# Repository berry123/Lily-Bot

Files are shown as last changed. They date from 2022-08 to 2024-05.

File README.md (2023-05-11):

# Flower-Bots
This GITHUB as well as the one on YouTube, Instructables, Hackster and Rose-Hulman (https://wordpress.rose-hulman.edu/berry123) will document my guidebook for members of academia to use open-source hardware for service, education, and research. It will describe the creation of an open-source mobile robot platform with the flexiblity and modularity for modification based upon experience level, educational, outreach, or research goals.

https://www.oshwa.org/2022/06/15/congratulations-to-the-open-hardware-trailblazers/

OSHWA recently announced a call for Open Hardware Trailblazer Fellows. Thanks to the generous support of the Alfred P. Sloan Foundation, OSHWA is taking a giant step towards expanding open source hardware in academia through the Open Hardware Trailblazer Fellows initiative. The one-year fellowship provides grants to individuals who are leading the way as open source hardware expands into academia. The fellows will document their experience of making open source hardware in academia to create a library of resources for others to follow.

Carlotta Berry is a professor and Dr. Lawrence J. Giacoletto Endowed Chair for Electrical and Computer Engineering at Rose-Hulman Institute of Technology (RHIT). She is one of a team of faculty who created the first multidisciplinary minor in robotics. She has two bachelor’s degrees in mathematics from Spelman College and electrical engineering from Georgia Institute of Technology. She has a master’s from Wayne State University and PhD from Vanderbilt University. Her research interests include robotics education, human-robot interaction, and increasing marginalized and minoritized populations in STEM fields. Berry is a prolific speaker and author of the text, “Mobile Robotics for Multidisciplinary Study”. Berry is also the founder and co-director of the Rose Building Undergraduate Diversity (ROSE-BUD) Program and advisor for the National Society of Black Engineers. She was previously the President of the Technical Editor Board for the American Society of Engineering Education (ASEE) Computers in Education Journal, ASEE fellow and IEEE senior fellow. She has a special passion for diversifying the engineering profession by encouraging more women, marginalized and minoritized populations to pursue STEM degrees. She achieves this purpose with robotics education, engineering education and human-robot interaction research to bring more people to STEM. Her strong service record has garnered her multiple accolades and awards including 2023 IEEE Undergraduate Teaching Award, Society of Women Engineers 2022 Distinguished Engineering Educator Award, 2022 Distinguished Educator Award from the American Society of Engineering Education Electrical and Computer Engineering Division, 2022 Open Source Hardware Trailblazer Fellow, 2021 TechPoint Foundation for Youth Bridge Builder award, one of 30 Women in Robotics You Need to Know About 2020 by robohub.org, Reinvented Magazine Interview of the Year Award on Purpose and Passion, FIRST Indiana Robotics Gamechanger Award 2020, Women and Hi Tech Leading Light You Inspire Me Award 2018 and Insight Into Diversity Inspiring Women in STEM. During 2020, she worked with colleagues around the world to start two non-profit organizations, Black In Engineering and Black In Robotics. They have a mission to bring awareness to systemic racism and inequity in STEM, build community, advocate for diversity, equity, inclusion, justice, and connect with allies and sponsors.

oshw_facts

This project is certified open hardware.

OSHW Certified_xsmall

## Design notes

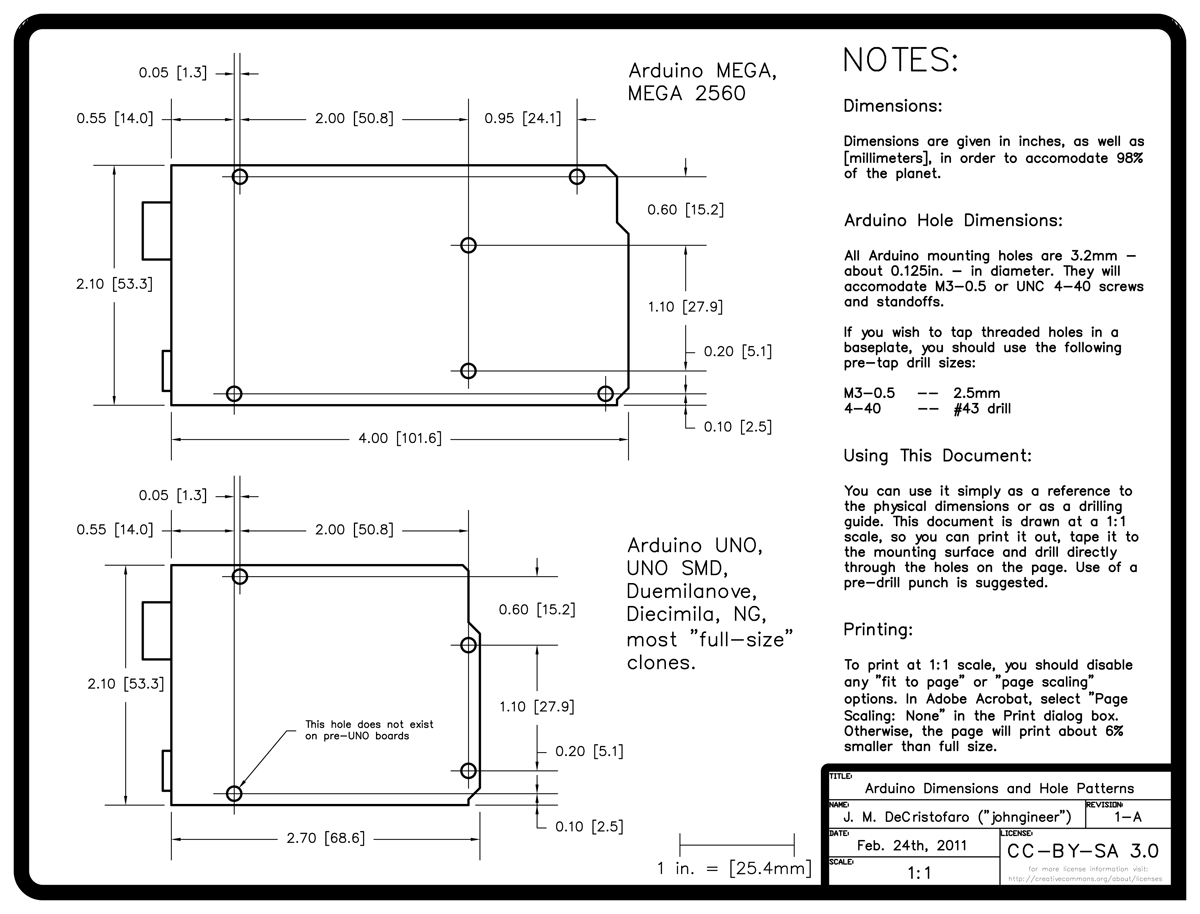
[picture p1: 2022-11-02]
Flower bots/Assembly/Uno and Mega schematics.png

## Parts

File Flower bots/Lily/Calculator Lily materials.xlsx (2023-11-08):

Input number of Lilys | 16
 |  | Part | Need | Have | Total |  | Part | Time/part (h) | Time to print (h) | Material/part (g) | Total material (g)
 | 3D Printer | Tops | 16 |  | 16 | 3D Printer | Tops | 3.50 | 56.00 | 37.36 | 597.76
 |  | Uno cover | 16 |  | 16 |  | Uno cover | 1.50 | 24.00 | 16.19 | 259.04
 |  | Bottom | 16 |  | 16 |  | Bottom | 5.00 | 80.00 | 53.36 | 853.76
 |  | Battery cover | 16 |  | 16 |  | Battery cover | 1.33 | 21.28 | 16.48 | 263.68
 |  | Motor mounts | 32 |  | 32 |  | Motor mount
 |  | Sonar mounts | 16 |  | 16 |  | Sonar mounts
 |  | (IR photo resistor mount | 16 |  | 16 |  | IR/photoresistor mounts
 |  | Standoffs | 64 |  | 64 |  | Standoffs | 0.43 | 27.71 | 2.29 | 146.496
 | Shopping | Motor controller | 32 |  | 32 |  | Total | - | 208.99 | - | 2120.736
 |  | Uno chip | 16 |  | 16
 |  | 9V battery holder | 16 |  | 16
 |  | Mini breadboards | 32 |  | 32
 |  | Caster wheels | 32 |  | 32
 |  | Motors | 32 |  | 32
 |  | Toy wheels | 32 |  | 32
 |  | Buzzers | 16 |  | 16
 |  | Sonar | 16 |  | 16
 |  | Male wires | 0
 |  | Female wires | 0
 |  | LEDs | 64 |  | 64
 |  | 220 Resistors | 64 |  | 64
 |  | photoresistors | 16 |  | 16
 |  | 10K resistors | 16 |  | 16

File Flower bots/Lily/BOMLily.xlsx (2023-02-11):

Part ID# | Product | Qty. | Price ind | Price total | Link
# | Upper Chassis | 1 | 7.00 | 7.00
# | Lower Chassis | 1 | 1.17 | 1.17
# | Standoffs | 4 | 1.62 | 6.48
 | TB6612 Motor Driver | 1 |  | 0.00
 | Arduino Uno | 1 | 6.26 | 6.26
 | Mini Breadboard | 2 |  | 0.00
# | Motor Mounts | 2 |  | 0.00
 | Toy Motors | 2 |  | 0.00
 | Toy Tire Wheels | 2 |  | 0.00
 | 5AA Battery Holder | 1 |  | 0.00
 | Cinch strap | 1 |  | 0.00
 | Caster Wheels 5/8” | 2 |  | 0.00
# | Sonar Mounts* | 2 |  | 0.00
 | HC-SR04 Sonar * | 1 |  | 0.00
# | IR Mounts* | 1 |  | 0.00
 | Sharp IR Sensor* | 1 |  | 0.00
 | LEDs* | 4 |  | 0.00
 | Buzzer* | 1 |  | 0.00
 | Slider Switch* | 1 |  | 0.00
 | Photoresistor* | 1 |  | 0.00
 | 10kΩ resistor* | 1 |  | 0.00
 | 100Ω resistor* | 4 |  | 0.00
 | Various Wires (Male-Male, Male-Female) | 20 |  | 0.00
 | 6mm panhead screws | 2 |  | 0.00
 | 8 mm panhead screws | 8 |  | 0.00
 | 25mm panhead screws | 2 |  | 0.00
 | Phillips head screwdriver | 1 |  | 0.00
 |  |  | Total: | 20.91

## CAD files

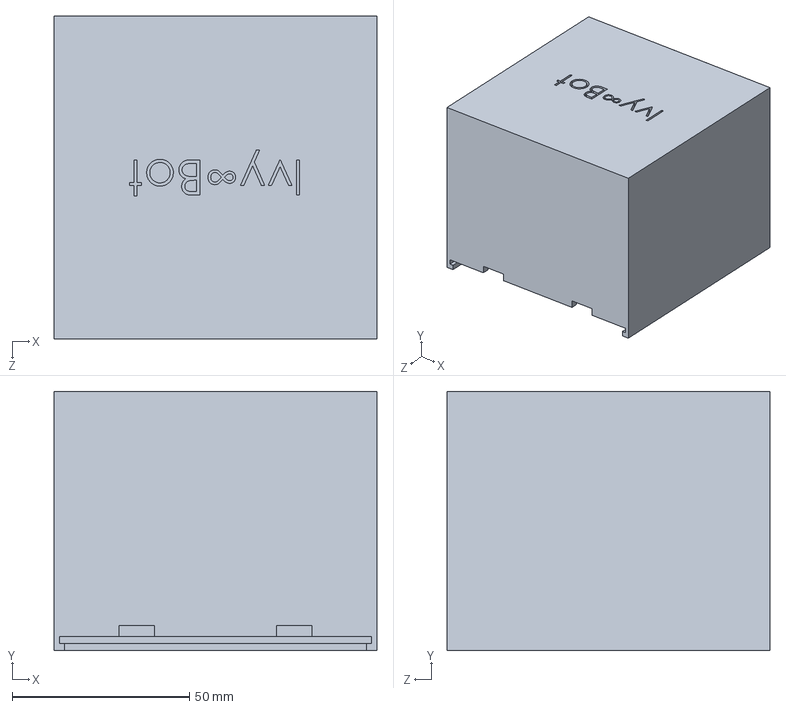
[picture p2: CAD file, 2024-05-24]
Flower bots/Ivy bot/Main box.SLDPRT
91.0 x 73.0 x 91.0 mm

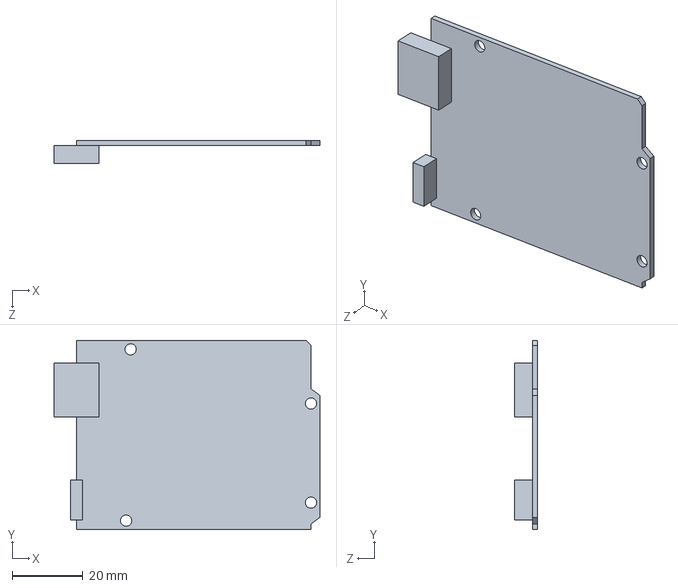
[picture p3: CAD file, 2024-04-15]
Flower bots/Assembly/Uno chip.SLDPRT
74.9 x 53.3 x 6.58 mm

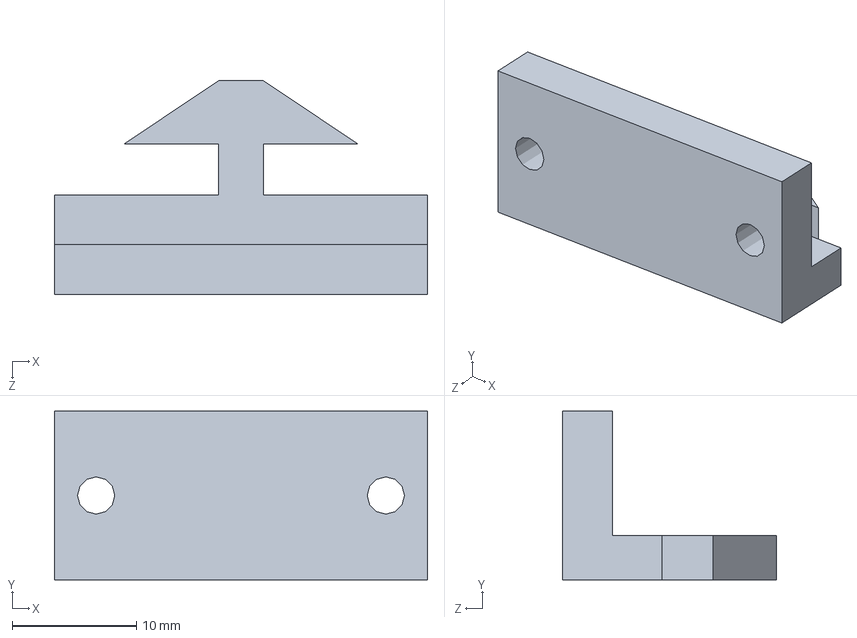
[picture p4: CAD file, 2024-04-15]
Flower bots/Attachments/SolidWorks/Gripper attachment.SLDPRT
30.0 x 13.6 x 17.2 mm

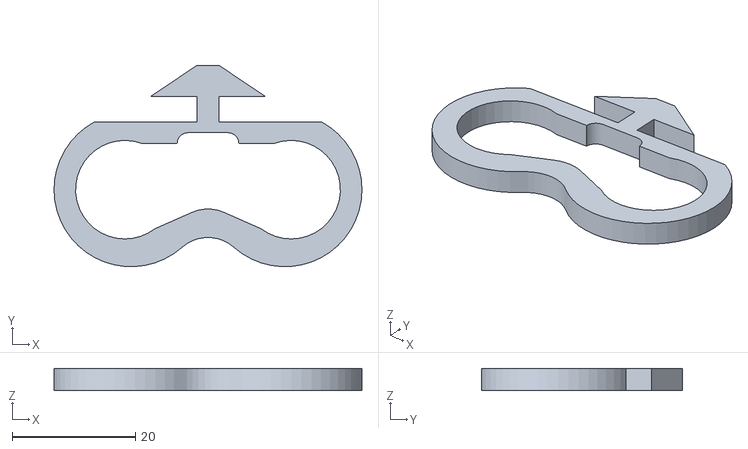
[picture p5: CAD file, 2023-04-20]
Flower bots/Attachments/STL/Sonar sensor Attachment .STL
50.0 x 32.7 x 3.58

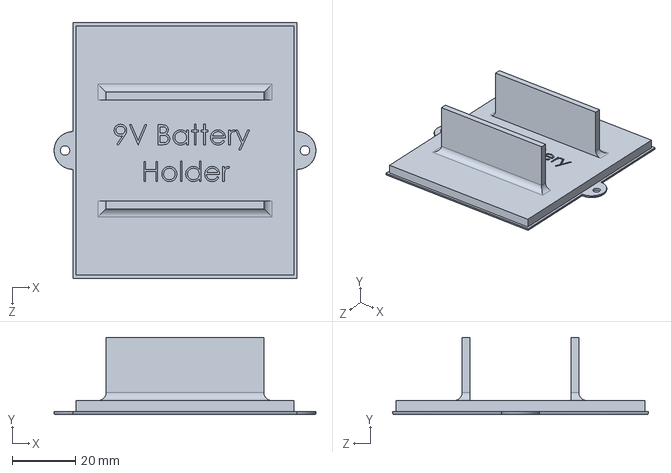
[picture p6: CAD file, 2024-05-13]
Flower bots/Battery modules/SolidWorks/9V Battery Holder New.SLDPRT
83.0 x 24.5 x 81.0 mm

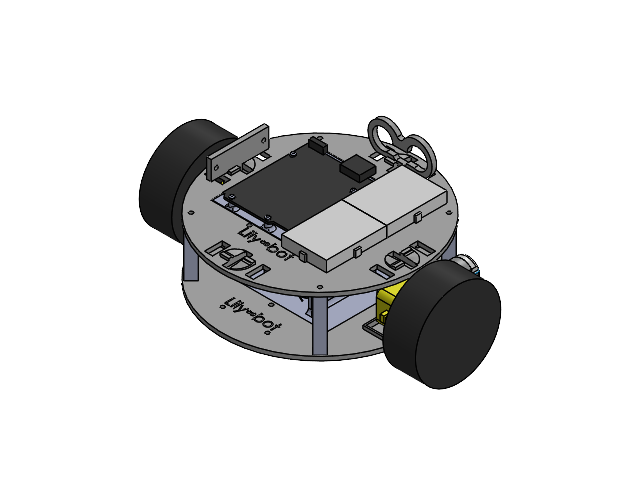
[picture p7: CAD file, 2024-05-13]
Flower bots/Lily/SolidWorks/LilyBot.SLDASM
Lily top Flex
Small breadboard x 2
Uno chip
Lily standoffs x 4
IR sensor Attachment
Sonar Attachment
Lily Bottom Flex_V2
Wheel x 2
9V Battery Holder New
Uno_Module_Snap
TT Motor.step x 2

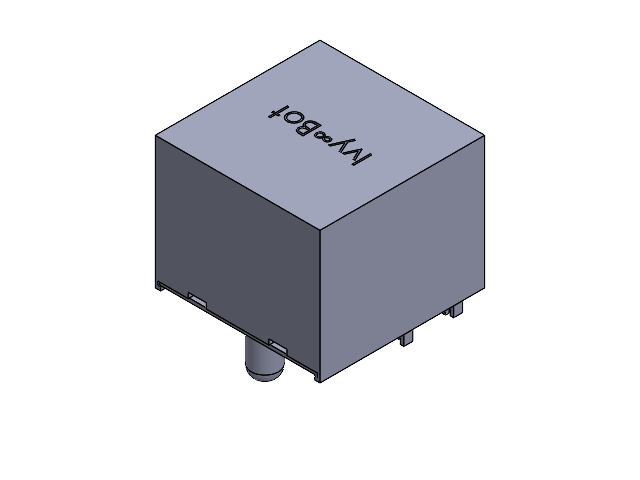
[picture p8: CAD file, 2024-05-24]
Flower bots/Ivy bot/IvyBot.SLDASM
Main box
Lid

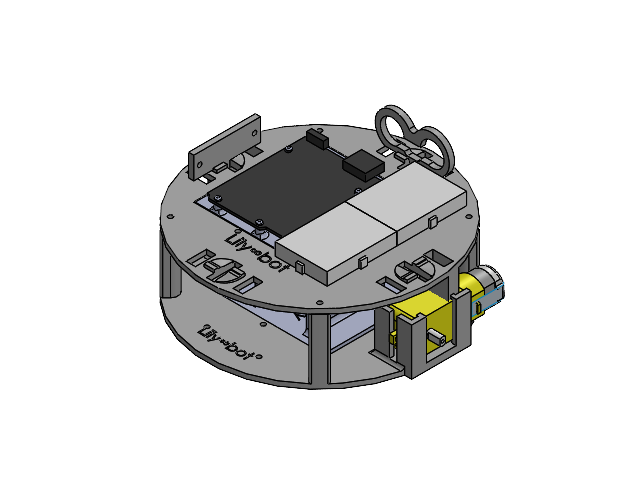
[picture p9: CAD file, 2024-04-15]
Flower bots/Lily/SolidWorks/LilyBot - Reduced Hardware.SLDASM
Lily top Flex V2
Small breadboard x 2
Uno chip
IR sensor Attachment
Sonar Attachment
Lily Bottom Flex V5
9V Battery Holder New
Uno_Module_Snap
TT Motor.step x 2

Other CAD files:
Flower bots/Jetson Nano version/142-13448-1000-A02_ASM.step.SLDASM
Flower bots/Jetson Nano version/142-13448-1000-A02-SKU0000_ASM.step.SLDASM
Flower bots/Jetson Nano version/Jetson nano_fixed.step.SLDASM
Flower bots/Jetson Nano version/PORG_HSK_ASSY_ASM.step.SLDASM
Flower bots/Jetson Nano version/Intel RealSense T265.step.SLDASM
Flower bots/Jetson Nano version/244-63448-0000-000_ASM.step.SLDASM
Flower bots/Jetson Nano version/142-13449-1000-A02_ASM.step.SLDASM
Flower bots/Attachments/STL/Gripper/GripperAttachment.STL
Flower bots/Battery modules/Printer/8x9V Battery Bambu.gcode.3mf
Flower bots/Battery modules/Stl/9V Battery Holder.STL
Daisy-Bottom STL.obj
Flower bots/Assembly Figures/Small breadboard.SLDPRT
Flower bots/Assembly Figures/TT Motor.step.SLDPRT
Flower bots/Assembly Figures/Uno chip.SLDPRT
Flower bots/Assembly Figures/Wheel.SLDPRT
Flower bots/Assembly/Caster Ball Wheel.STEP
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

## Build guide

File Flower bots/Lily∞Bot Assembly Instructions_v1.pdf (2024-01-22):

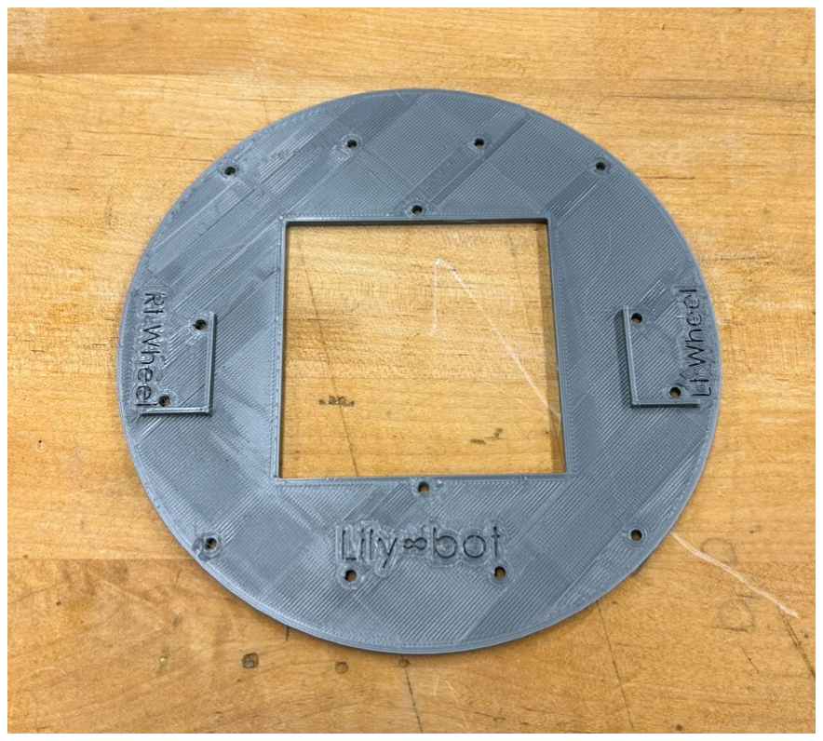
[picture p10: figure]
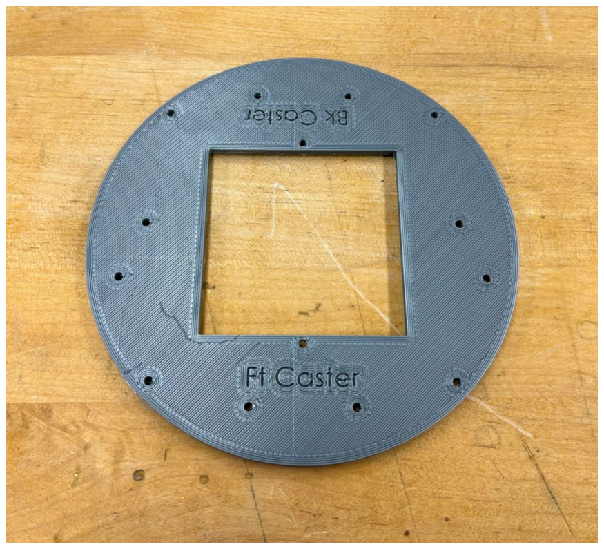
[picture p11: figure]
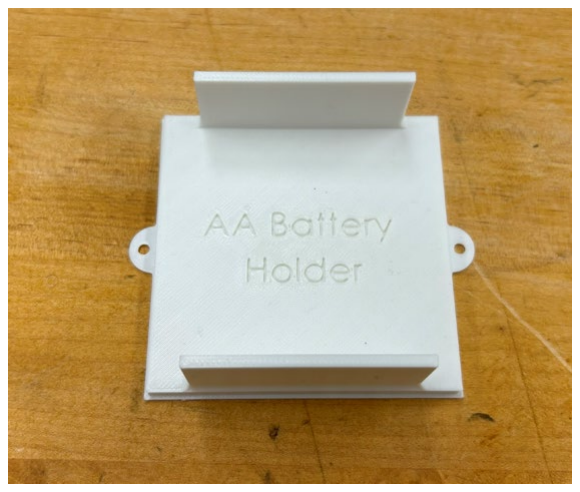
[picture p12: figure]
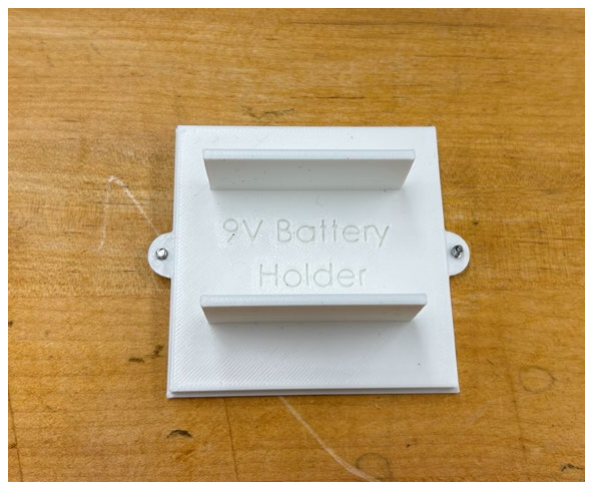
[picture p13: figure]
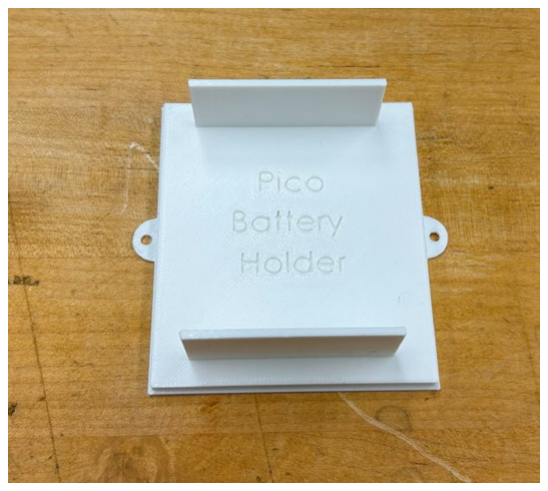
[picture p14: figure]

Version 1: 12/1/23 | Building Lily∞Bot | 1

# Building Lily∞Bot

1. Start by laying out the bottom of the chassis and the battery module that corresponds to your

controller. The AA battery holder is for the Arduino Uno, the 9V battery holder is for the

Microbit, and the Pico battery holder is for the Raspberry Pi Pico.

Figure 1: Top (left) and bottom (right) faces of the bottom chassis

Figure 2: AA Battery holder for the Arduino Uno, 9V battery holder for the Microbit, and the battery

holder for the Raspberry Pi Pico
2. Now that you have your bottom chassis and the right battery holder, let’s start assembling.

This guide uses the 9V battery pack module for its robot. Place your bottom chassis with the

Rt Motor and Lt Motor text facing up and the Ft Caster and Bk Caster text facing down. Take your battery holder and slot it into the chassis from the bottom such that the mounting holes

line up with the holes in the chassis. Figure 3 shows the robot base with a 9V battery pack

module screwed into it.

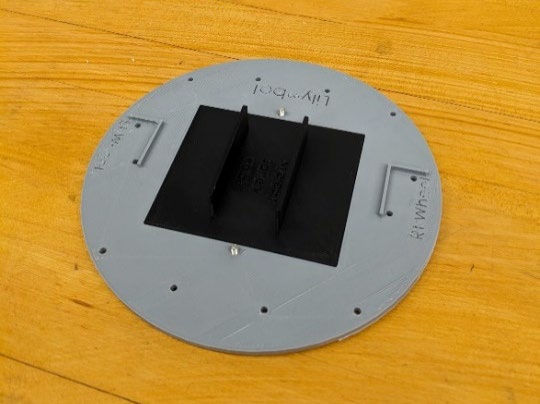
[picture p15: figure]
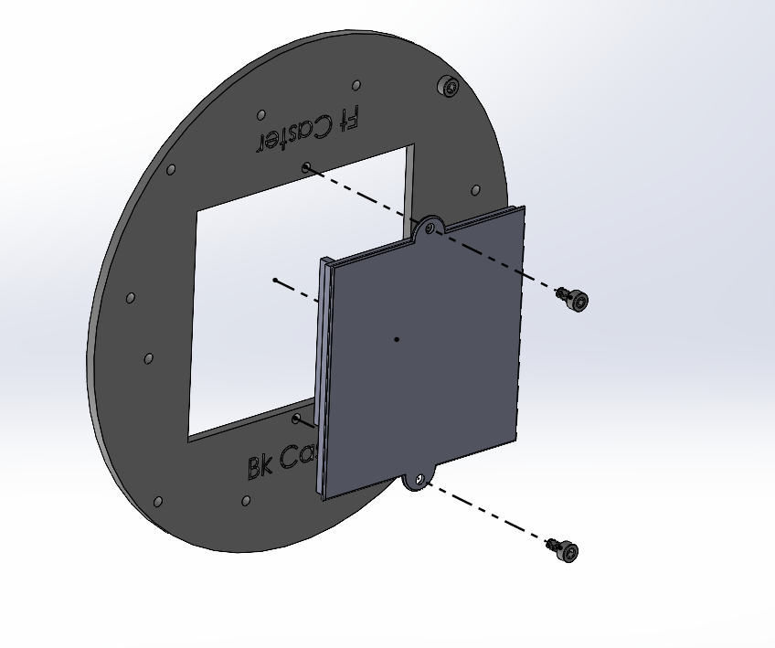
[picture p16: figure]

Figure 3: Bottom base with battery pack module.
3. Get the left and right 3d printed motor mounts and the 2 motors. If not attached, you will

need to use two 10 mm (about 0.39 in) M3 machine screws to attach each motor to the motor

mount. Make sure that the red and black wires point toward the long-slotted end of the

motor mount. Figure 4 shows the right and left motors inserted into the motor mounts with

the 10 mm screws. The figure also shows 2 wheels and four 8 mm (about 0.31 in) M3

mounting screws for attaching the motor mount to the base of the robot.

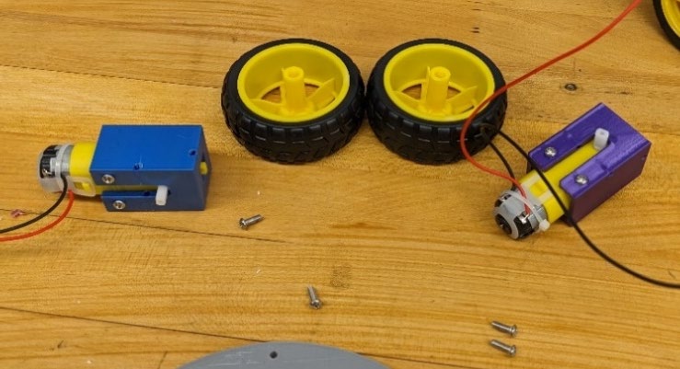
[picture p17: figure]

Figure 4: Wheels, Motors, and Screws.

4. Figure 5 shows the various batteries inserted into their corresponding battery holders. Each

battery pack may be inserted at any time during the robot assembly process. Note that the

robot will ship without batteries.

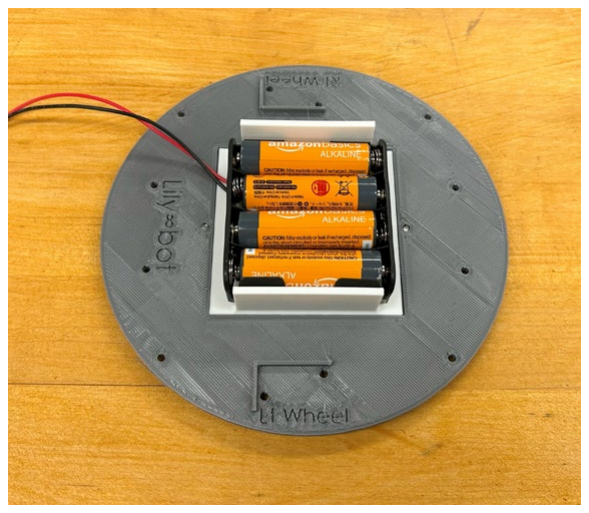
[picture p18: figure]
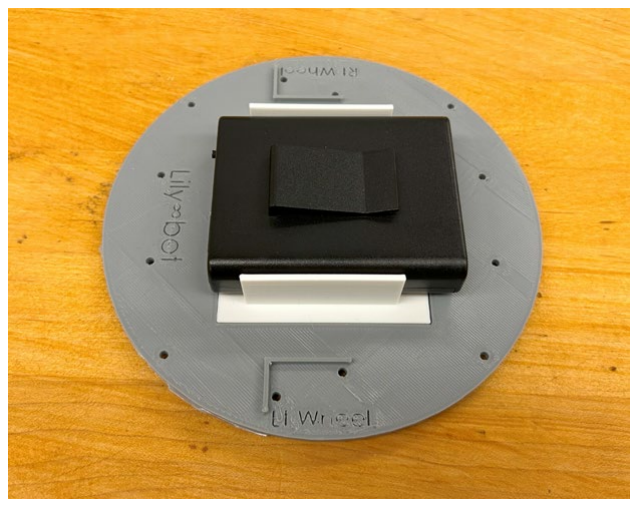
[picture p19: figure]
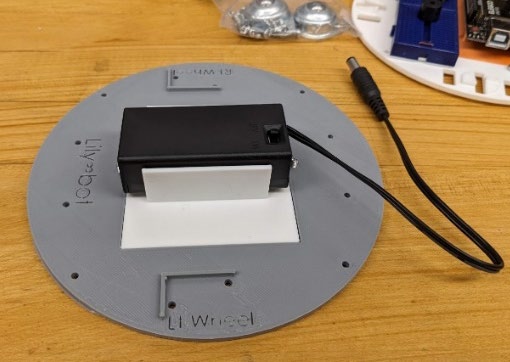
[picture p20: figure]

Figure 5: 9V, Pico, and AA battery packs inserted in battery pack module on robot base
5. The side of each motor should have either an R or an L engraved on it. Starting with the left

motor, place it on the left side of the base (also engraved) such that the wires face the inside

of the robot and the mounting holes on the motor line up with the base. Take one of your

mounting screws, and, using a Phillips head screwdriver, thread it into the bottom of the base

until the head is flush with the base. Repeat with the other screw until the motor is securely

in place. Repeat with the other motor. Figure 6 shows mounting the motors to the robot base.

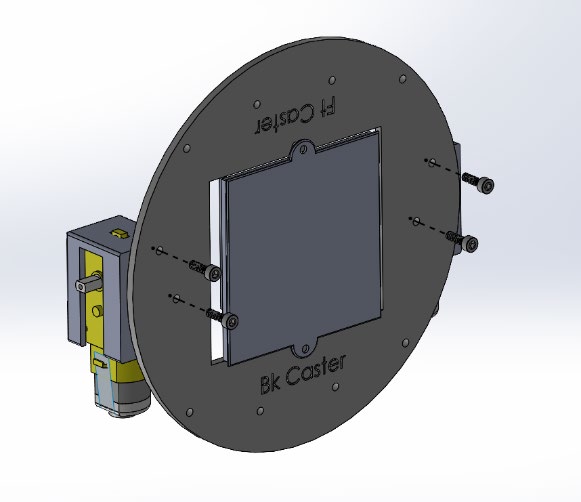
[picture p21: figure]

Figure 6: Attaching the motors to the robot base.
6. Collect 2 caster wheels, 4 M3 screws, 4 M3 nuts, and 4 M3 lock washers as shown in Figure

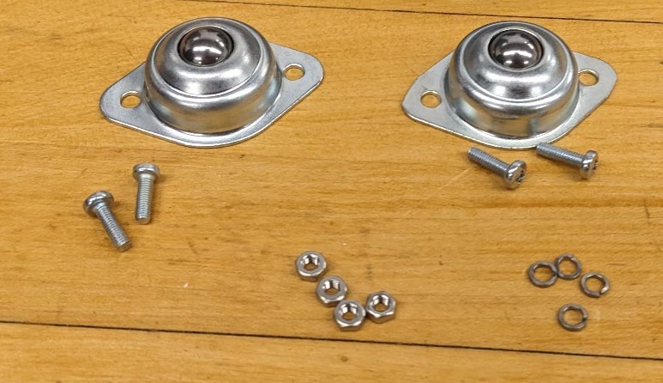
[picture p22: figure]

Figure 7: 2 caster wheels, 4 M3 8 mm (about 0.31 in) screws, 4 M3 lock washers, 4 M3 washers
7. Mount the front caster wheel (labeled on bottom of base) by taking the wheel and placing its

flat side against the bottom of the base. Take each screw and push it through the wheel and

base. Take your lock washer (one for each screw) and place it on the screw. Finally, thread

the nut onto the screw, using a Phillips head screwdriver and appropriate wrench to firmly

secure the wheel in place. Repeat with back caster wheel. Figure 8 shows the steps to attach

the two cater wheels to the bottom robot chassis.

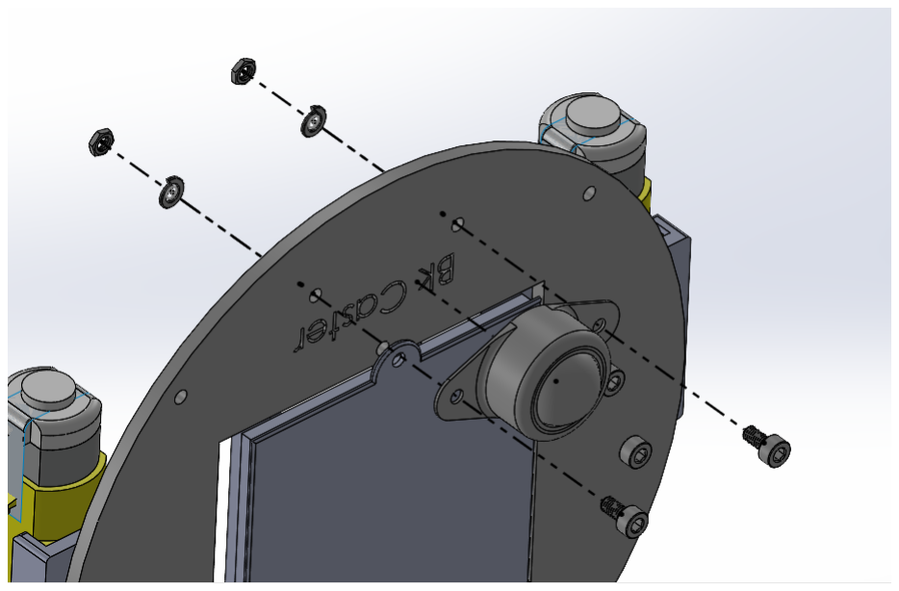
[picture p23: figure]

Figure 8: Attach the caster wheel to the bottom robot chassis using 2 screws, 2 nuts, and 2 lock washers
8. Collect 4 standoffs and 4 8mm (about 0.31 in) M3 machine screws as shown in Figure 9.

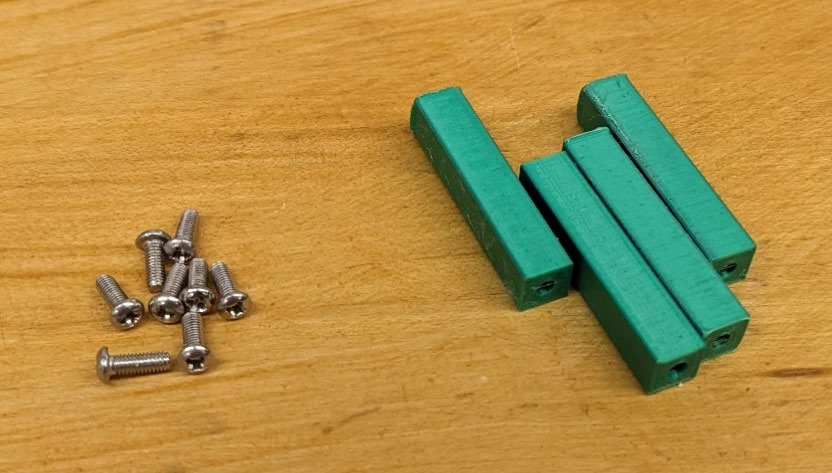
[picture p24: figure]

Figure 9: 4 standoffs and 8 8 mm M3 screws
9. Take one standoff and position it above one of the 4 holes on the outside of the bottom

piece. Take one screw and thread it through the hole, into the standoff from the bottom

of the base. Screw it in carefully, making sure the screw is perpendicular to the base. If

you feel too much resistance, take it out and try again making sure the screw is straight.

Figure 10 shows an example of connecting one standoff to the robot bottom chassis.

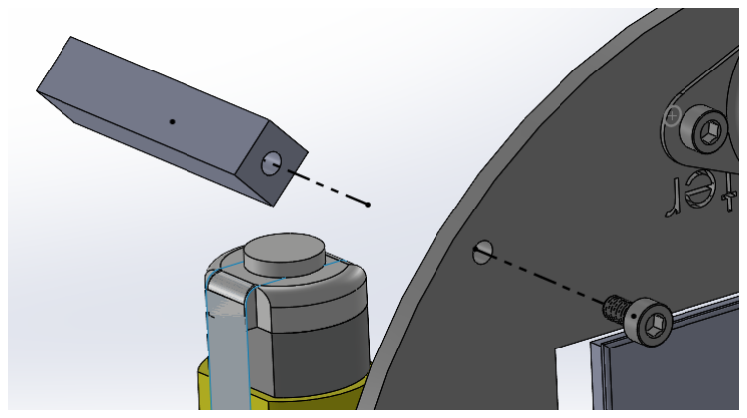
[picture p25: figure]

Figure 10: Connect one standoff to the robot bottom chassis with an 8 mm M3 screw
10. Repeat with the other standoffs, only screwing them in from the base. You should have

4 screws left over when you are done.

11. Retrieve the top chassis for the robot as shown in Figure 11 and attach the

corresponding controller module to it using 2 screws.

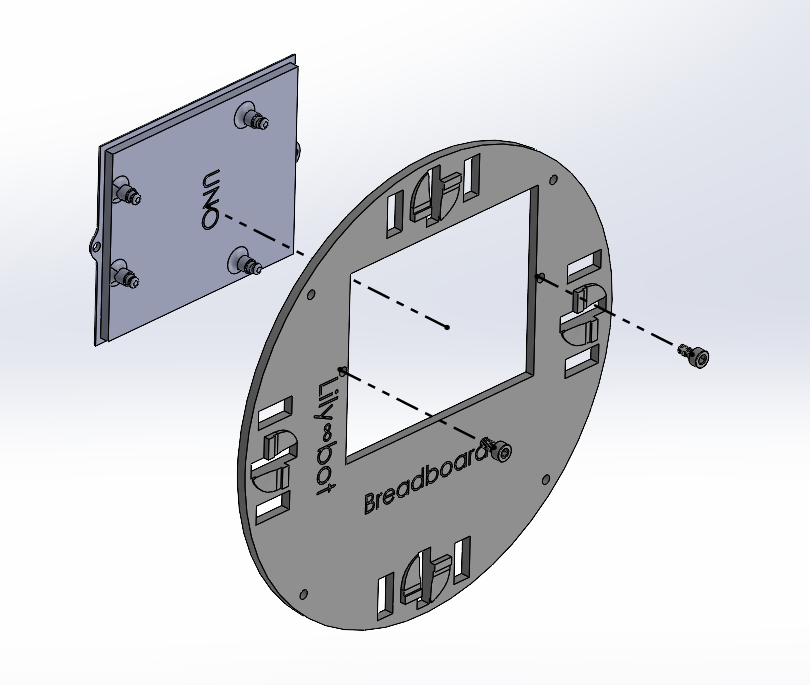
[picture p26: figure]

Figure 11: Screwing the controller mount into the top chassis
12. Some Pico and Uno controller mounts are snap-ons and some have holes to screw into.

For the former, carefully snap the controller in place, lining the holes of the controller

with the mounts and pressing slowly. For the latter, use two 6 mm screws to mount the

controller. Figure 12 shows the Pico and Uno attached to the module with screws.

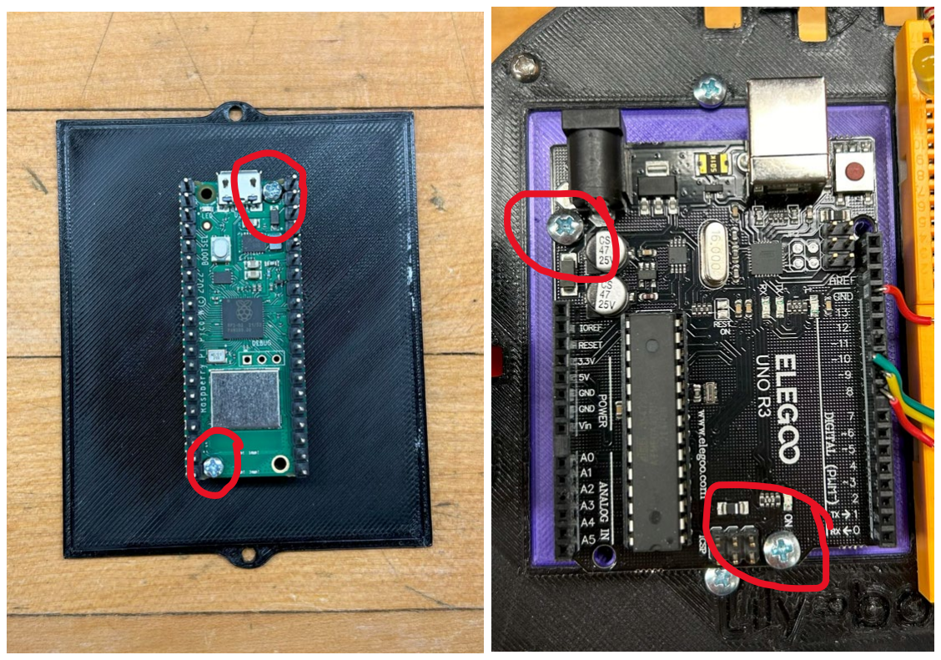
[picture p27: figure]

Figure 12: Pico and Uno microcontrollers screwed into their mounts

13. To install the Microbit, you need to carefully slide the board into the two grooves on the

mount. Push it through such that the board is roughly centered on the mount. Then attach

the vertical board by slotting it into the gold end of the horizontal board.

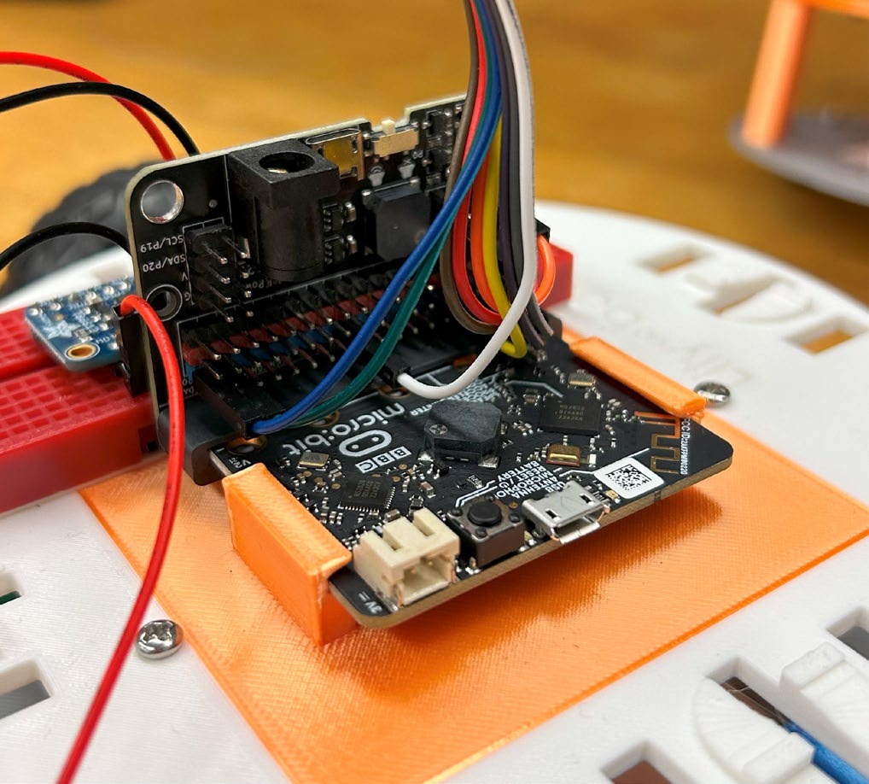
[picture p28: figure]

Figure 13: Installed Microbit controller
14. Next, attach two mini breadboards to the side of the module as shown in Figure 14.

Make sure to not cover any of the sensor or standoff mounting holes.

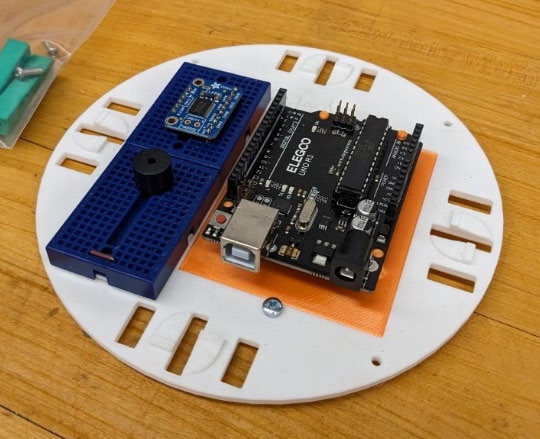
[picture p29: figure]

Figure 14: Upper robot chassis with microcontroller mount, microcontroller, two breadboards, and

TB6612 motor controller installed in breadboard

15. Use the four screws to attach the robot upper chassis to the four standoffs. Make sure

the text is aligned so that the words Lily∞Bot are above each other facing the same

direction. Figure 10 shows the attachment of the four screws to the robot.

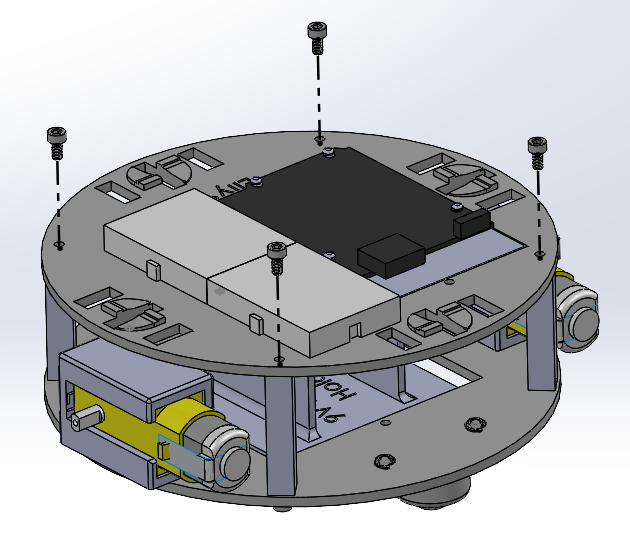
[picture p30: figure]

Figure 15: Attach the robot upper chassis to the bottom chassis with the 4 M3 8 mm machine screws

and standoffs.
16. Finally, attach the two wheels to the DC motors as shown in Figure 16.

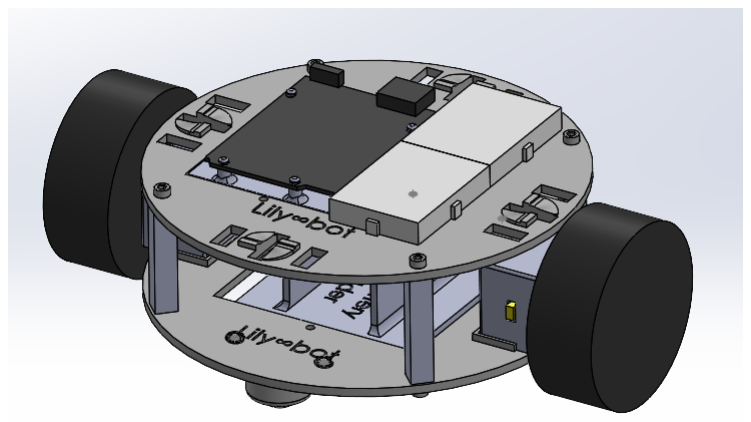
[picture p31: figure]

Figure 16: Two wheels attached to two DC motors on side of Lily∞Bot

# Congratulations Lily∞Bot is Built!

References:

GitHub: | https://github.com/berry123/Lily-Bot
HacksterIO: | https://www.hackster.io/berry123
Instructables: | https://www.instructables.com/member/carlottaberry/
Website: ￼ | https://www.noiresteminist.com/shop
YouTube: | https://www.youtube.com/playlist?list=PL175eO9NwPXICoPyAxInbduXcNKWURqm_

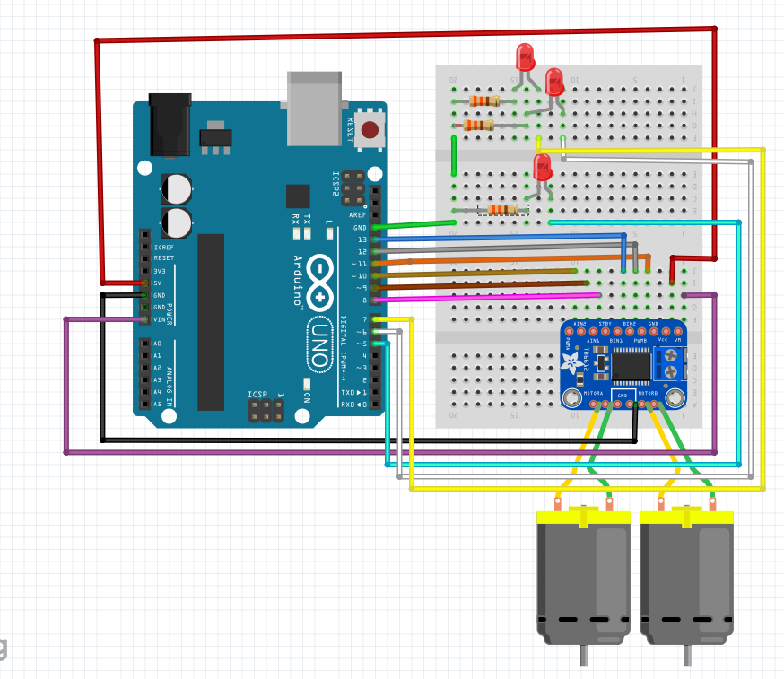
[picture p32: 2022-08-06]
Lily-Motor&LedWiring.PNG

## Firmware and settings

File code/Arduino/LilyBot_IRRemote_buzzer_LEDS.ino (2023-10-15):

/*
  Lily∞Bot Basic Motion Control
  LilyBot-BasicMotion.ino
  Control 2 DC motors with TB6612 motor controller (https://www.adafruit.com/product/2448)
  This program will create low level motion control: forward, reverse, spin, turn, pivot, stop

  Carlotta A. Berry, PhD
  April 7, 2023
  Katie Collins
  5/11/23
  Hardware Connections:

    TB6612 Motor Driver
      Vmotor - voltage for the motors, not logic level (4.5-13.5V)
  Vcc - voltage for the logic levels (Arduinos, 5V)
  GND - shared logic and motor ground
    Arduino pin 8 AIN1
    Arduino pin 9 AIN2
    Arduino pin 10 PWMA
    Arduino pin 5 PWMB
    Arduino pin 6 BIN2
    Arduino pin 7 BIN1
    Arduino GND GND
    Arduino 5V Vcc
    Arduino VIN Vm
    Left Motor Motor A (Red, Black)
    Right Motor Motor B (Red, Black)

    Buzzer pin A3
    Blue LED pin 2
    Green LED pin 12
    Yellow LED pin 4
    Read LED pin 3
*/
#include "IRremote.h"

int ftreceiver = 11;  // Front IR Receiver

// /*-----( Declare objects )-----*/
IRrecv ftirrecv(ftreceiver);  // create instance of 'irrecv'
decode_results ftresults;     // create instance of 'decode_results'


//the left motor will be controlled by the motor A pins on the motor driver
const int AIN1 = 8;   //control pin 1 on the motor driver for the left motor
const int AIN2 = 9;   //control pin 2 on the motor driver for the left motor
const int PWMA = 10;  //speed control pin on the motor driver for the left motor

//the right motor will be controlled by the motor B pins on the motor driver
const int PWMB = 5;  //speed control pin on the motor driver for the right motor
const int BIN2 = 6;  //control pin 2 on the motor driver for the right motor
const int BIN1 = 7;  //control pin 1 on the motor driver for the right motor


//robot behaviour variables
int moveTime = 500;    //amount of time robot will move
int robotSpeed = 150;  //robot speed


#define buzzerPin A3
#define bluLED 2
#define grnLED 12
#define ylwLED 4
#define redLED 3
int ledPins[4] = { 12, 2, 3, 4 };  //LED pins

//song variables
const int songLength = 18;
int tempo = 113;

//note for songs
char notes[songLength] = {
  'c', 'd', 'f', 'd', 'a', ' ', 'a', 'g', ' ', 'c', 'd', 'f', 'd', 'g', ' ', 'g', 'f', ' '
};

//beats for songs
int beats[songLength] = {
  1, 1, 1, 1, 1, 1, 4, 4, 2, 1, 1, 1, 1, 1, 1, 4, 4, 2
};


int i, duration;
int j;
const int numNotes = 8;  // number of notes we're storing
char names[numNotes] = {
  'c', 'd', 'e', 'f', 'g', 'a', 'b', 'C'
};
int octave = 2;
int frequencies[numNotes] = {
  262 * octave - 1, 294 * octave - 1, 330 * octave - 1, 349 * octave - 1, 392 * octave - 1, 440 * octave - 1, 494 * octave - 1, 523 * octave - 1
};

/*runs only once at beginning******/
void setup() {
  Serial.begin(9600);  //start serial communication
  Serial.println("Lily∞Bot IR Remote Drive");
  ftirrecv.enableIRIn();  // Start the receiver
  configurePins();        //set pins as inputs and outputs
}

/*----( LOOP: RUNS CONSTANTLY )----*/
void loop() {
  if (ftirrecv.decode(&ftresults))  // have we received an IR signal?
  {
    Serial.println("front received");
    translateIR(ftresults);
    ftirrecv.resume();  // receive the next value
  }
  delay(100);
  //Serial.println("Back in loop");
} /* --(end main loop )-- */


/************************* HELPER FUNCTIONS *********************/
// set the pins as inputs and outputs
void configurePins() {
  pinMode(AIN1, OUTPUT);
  pinMode(AIN2, OUTPUT);
  pinMode(PWMA, OUTPUT);
  pinMode(BIN1, OUTPUT);
  pinMode(BIN2, OUTPUT);
  pinMode(PWMB, OUTPUT);
  pinMode(ftreceiver, INPUT);
  pinMode(buzzerPin, OUTPUT);
  pinMode(bluLED, OUTPUT);
  pinMode(grnLED, OUTPUT);
  pinMode(ylwLED, OUTPUT);
  pinMode(redLED, OUTPUT);
}

//translate the IR signal into a robot ehavior based upon button pressed
void translateIR(struct decode_results results) {
  switch (results.value) {
    case 0xFFA25D:
      Serial.println("POWER");
      spin2();
      delay(moveTime);
      stop();
      break;
    case 0xFFE21D:
      Serial.println("FUNC/STOP");
      spin();
      delay(moveTime);
      stop();
      break;
    case 0xFF629D:
      Serial.println("VOL+");
      forward();
      delay(moveTime);
      stop();
      break;
    case 0xFF22DD:
      Serial.println("FAST BACK");
      turn();
      delay(moveTime);
      stop();
      break;
    case 0xFF02FD:
      Serial.println("PAUSE");
      play_song();
      Serial.println("Break");
      break;
    case 0xFFC23D:
      Serial.println("FAST FORWARD");
      turn2();
      delay(moveTime);
      stop();
      break;
    case 0xFFE01F:
      Serial.println("DOWN");
      pivot();
      delay(moveTime);
      stop();
      break;
    case 0xFFA857:
      Serial.println("VOL-");
      reverse();
      delay(moveTime);
      stop();
      break;
    case 0xFF906F:
      Serial.println("UP");
      pivot2();
      delay(moveTime);
      stop();
      break;
    case 0xFF6897:
      Serial.println("0");
      ALL_LEDS_ON();
      delay(moveTime);
      ALL_LEDS_OFF();
      break;
    case 0xFF30CF:
      Serial.println("1");
      ylwLedOn();
      delay(moveTime);
      ylwLedOff();
      break;
    case 0xFF18E7:
      Serial.println("2");
      redLedOn();
      delay(moveTime);
      redLedOff();
      break;
    case 0xFF7A85:
      Serial.println("3");
      bluLedOn();
      delay(moveTime);
      bluLedOff();
      break;
    case 0xFF10EF:
      Serial.println("4");
      grnLedOn();
      delay(moveTime);
      grnLedOff();
      break;
    case 0xFF9867: Serial.println("EQ"); break;
    case 0xFFB04F: Serial.println("ST/REPT");  break;
    case 0xFF38C7: Serial.println("5"); break;
    case 0xFF5AA5: Serial.println("6"); break;
    case 0xFF42BD: Serial.println("7"); break;
    case 0xFF4AB5: Serial.println("8"); break;
    case 0xFF52AD: Serial.println("9"); break;
    default:
      Serial.println(results.value);
      break;
  }            //end switch case
  delay(250);  // Do not get immediate repeat
}

// ************************************ Motor Functions *****************************


//robot stop function
void stop() {
  setRightMotorStop();
  setLeftMotorStop();
}

//robot forward function
void forward() {
  setRightMotorForward();
  setLeftMotorForward();
  //set motor speeds
  analogWrite(PWMA, abs(robotSpeed));  //set forward speed
  analogWrite(PWMB, abs(robotSpeed));  //set forward speed
}

//robot reverse function
void reverse() {
  setRightMotorBackward();
  setLeftMotorBackward();
  //set motor speeds
  analogWrite(PWMA, abs(robotSpeed));  //set reverse speed
  analogWrite(PWMB, abs(robotSpeed));  //set reverse speed
}

//robot pivot function
void pivot() {
  setRightMotorStop();
  setLeftMotorForward();
  //set motor speeds
  analogWrite(PWMB, abs(robotSpeed));  //set forward speed
}


//robot pivot function
void pivot2() {
  setRightMotorForward();
  setLeftMotorStop();
  //set motor speeds
  analogWrite(PWMA, abs(robotSpeed));  //set forward speed
}

//robot turn function
void turn() {
  setRightMotorForward();
  setLeftMotorForward();
  //set motor speeds
  analogWrite(PWMA, abs(robotSpeed));        //set forward speed
  analogWrite(PWMB, abs(0.7 * robotSpeed));  //set forward speed
}

//robot turn function
void turn2() {
  setRightMotorForward();
  setLeftMotorForward();
  //set motor speeds
  analogWrite(PWMA, abs(0.7 * robotSpeed));  //set forward speed
  analogWrite(PWMB, abs(robotSpeed));        //set forward speed
}

//robot spin function
void spin() {
  setRightMotorBackward();
  setLeftMotorForward();
  //set motor speeds
  analogWrite(PWMA, abs(robotSpeed));  //set reverse speed
  analogWrite(PWMB, abs(robotSpeed));  //set forward speed
}

//robot spin function
void spin2() {
  setRightMotorForward();
  setLeftMotorBackward();
  //set motor speeds
  analogWrite(PWMA, abs(robotSpeed));  //set forward speed
  analogWrite(PWMB, abs(robotSpeed));  //set reverse speed
}

void setRightMotorForward() {
  digitalWrite(AIN1, LOW);   //set pin 1 to low
  digitalWrite(AIN2, HIGH);  //set pin 2 to high
}

void setLeftMotorForward() {
  digitalWrite(BIN1, LOW);   //set pin 1 to low
  digitalWrite(BIN2, HIGH);  //set pin 2 to high
}

void setRightMotorBackward() {
  digitalWrite(AIN1, HIGH);  //set pin 1 to high
  digitalWrite(AIN2, LOW);   //set pin 2 to low
}


void setLeftMotorBackward() {
  digitalWrite(BIN1, HIGH);  //set pin 1 to high
  digitalWrite(BIN2, LOW);   //set pin 2 to low
}

void setRightMotorStop() {
  digitalWrite(AIN1, LOW);  //set pin 1 to low
  digitalWrite(AIN2, LOW);  //set pin 2 to low
}

void setLeftMotorStop() {
  digitalWrite(BIN1, LOW);  //set pin 1 to low
  digitalWrite(BIN2, LOW);  //set pin 2 to low
}



// ************************************ Buzzer Functions *****************************


// play the song
void play_song() {
  //  int i, duration;  //
  Serial.println("\t play song");
  ftirrecv.stop();
  for (i = 0; i < songLength; i++) {  // for loop is used to index through the arrays
    duration = beats[i] * tempo;      // length of note/rest in ms
    digitalWrite(ledPins[i % 4], HIGH);
    if (notes[i] == ' ')  // is this a rest?

      delay(duration);  // then pause for a moment
    else                // otherwise, play the note
    {
      if (i % 2 == 0) {  // robot spins a different direction on each note
        spin();          // robot spins along with the music
      } else {
        spin2();
      }
      tone(buzzerPin, frequency(notes[i]), duration);
      delay(duration * 1.4);  // wait for tone to finish
      stop();
    }
    delay(tempo / 10);  // brief pause between notes
    ALL_LEDS_OFF();
  }
  ftirrecv.start();
}

//set the note frequencies
int frequency(char note) {
  for (j = 0; j < numNotes; j++)  // Step through the notes
  {
    if (names[j] == note)  // Is this the one?
    {
      return (frequencies[j]);  // Yes! Return the frequency and exit function.
    }
  }
  return (0);
}


// ************************************ LED Functions *****************************

// will turn on the green LED
void grnLedOn() {
  digitalWrite(grnLED, HIGH);
}

// will turn off green LED
void grnLedOff() {
  digitalWrite(grnLED, LOW);
}

// will turn on the yellow LED
void ylwLedOn() {
  digitalWrite(ylwLED, HIGH);
}

// will turn off yellow LED
void ylwLedOff() {
  digitalWrite(ylwLED, LOW);
}

// will turn on the red LED
void redLedOn() {
  digitalWrite(redLED, HIGH);
}

// will turn off red LED
void redLedOff() {
  digitalWrite(redLED, LOW);
}

// will turn on the blue LED
void bluLedOn() {
  digitalWrite(bluLED, HIGH);
}

// will turn off blue LED
void bluLedOff() {
  digitalWrite(bluLED, LOW);
}

// all LEDS OFF
void ALL_LEDS_OFF() {
  digitalWrite(bluLED, LOW);
  digitalWrite(grnLED, LOW);
  digitalWrite(ylwLED, LOW);
  digitalWrite(redLED, LOW);
}

// all LEDS ON
void ALL_LEDS_ON() {
  digitalWrite(bluLED, HIGH);
  digitalWrite(grnLED, HIGH);
  digitalWrite(ylwLED, HIGH);
  digitalWrite(redLED, HIGH);
}

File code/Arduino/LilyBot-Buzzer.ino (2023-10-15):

/*
  Lily∞Bot
  LilyBot-Buzzer.ino
  Carlotta A. Berry, PhD
  FEBRUARY 5, 2023

  This program will use the SparkFun Inventor's Kit version 3.0 buzzer code to show how to
  play music on the Lily∞Bot (see https://www.sparkfun.com/sikcode)


*/

//state LEDs
const int ledPins[4] = {4, 5, 6, 7 };
const int ylwLED = 4;
const int redLED = 5;
const int bluLED = 6;
const int grnLED = 7;


const int switchPin = 2;      //robot on-off switch
const int buzzerPin = 3;       //buzzer pin
const int photoresistor = A0;  //photoresistor pin


//the left motor will be controlled by the motor A pins on the motor driver
const int AIN1 = 8;  //control pin 1 on the motor driver for the left motor
const int AIN2 = 9;  //control pin 2 on the motor driver for the left motor
const int PWMA = 10;  //speed control pin on the motor driver for the left motor

//the right motor will be controlled by the motor B pins on the motor driver
const int PWMB = 11;  //speed control pin on the motor driver for the right motor
const int BIN1 = 12;  //control pin 1 on the motor driver for the right motor
const int BIN2 = 13;  //control pin 2 on the motor driver for the right motor


//robot behaviour variables
int moveTime = 2000;   //amount of time robot will move
int robotSpeed = 100;  //robot speed

//song variables
const int songLength = 18;
int tempo = 150;

char notes[songLength] = {
  'c', 'd', 'f', 'd', 'a', ' ', 'a', 'g', ' ', 'c', 'd', 'f', 'd', 'g', ' ', 'g', 'f', ' '
};

int beats[songLength] = {
  1, 1, 1, 1, 1, 1, 4, 4, 2, 1, 1, 1, 1, 1, 1, 4, 4, 2
};


/********************************************************************************/
void setup() {
  int baudrate = 9600;     //serial communication baud rate
  Serial.begin(baudrate);  //start serial commnication
  delay(100);
  //set switch as an input
  pinMode(switchPin, INPUT_PULLUP);
  //set LEDS as an output
  for (int i = 0; i < 4; i++) {
    pinMode(ledPins[i], OUTPUT);
  }
  // set buzzer as an output
  pinMode(buzzerPin, OUTPUT);

  //set photoresistor as an input
  pinMode(photoresistor, INPUT);

  //set the motor control pins as outputs
  pinMode(AIN1, OUTPUT);
  pinMode(AIN2, OUTPUT);
  pinMode(PWMA, OUTPUT);
  pinMode(BIN1, OUTPUT);
  pinMode(BIN2, OUTPUT);
  pinMode(PWMB, OUTPUT);

  //STARTING LIGHT SEQUENCE
  for (int i = 0; i < 4; i++) {
    //Serial.print(i);
    digitalWrite(ledPins[i], HIGH);
    delay(1000);
  }
  Serial.println();
  for (int i = 4; i > -1; i--) {
    //Serial.print(i);
    digitalWrite(ledPins[i], LOW);
    delay(1000);
  }
  Serial.print("Daisy∞bot begin");  //print start message
}

/********************************************************************************/
void loop() {
  int on = digitalRead(switchPin);
  Serial.print(" on = ");
  Serial.println(on);
  if (on == 1) {
    play_song();
  }
  if (on == 0) {
    Serial.println("Robot Off");
    stop();
  }
}
/************************* BUZZER FUNCTIONS *************************************/
// play the song
void play_song() {
  int i, duration;  //
  Serial.print("\t play song");

  for (i = 0; i < songLength; i++)  // for loop is used to index through the arrays
  {
    duration = beats[i] * tempo;  // length of note/rest in ms
    digitalWrite(ledPins[i%4],HIGH);
    if (notes[i] == ' ')  // is this a rest?
      delay(duration);    // then pause for a moment
    else                  // otherwise, play the note
    {
      tone(buzzerPin, frequency(notes[i]), duration);
      delay(duration);  // wait for tone to finish
    }
    delay(tempo / 10);  // brief pause between notes
    allLedsOff();
  }
}

//set the note frequencies
int frequency(char note) {
  int i;
  const int numNotes = 8;  // number of notes we're storing
  char names[numNotes] = {
    'c', 'd', 'e', 'f', 'g', 'a', 'b', 'C'
  };
  int frequencies[numNotes] = {
    262, 294, 330, 349, 392, 440, 494, 523
  };

  // Now we'll search through the letters in the array, and if
  // we find it, we'll return the frequency for that note.

  for (i = 0; i < numNotes; i++)  // Step through the notes
  {
    if (names[i] == note)  // Is this the one?
    {
      return (frequencies[i]);  // Yes! Return the frequency and exit function.
    }
  }
  return (0);
}

/********************************* MOTION FUNCTIONS ******************************/
//robot stop function
void stop() {
  allLedsOff();
  //left motor stop
  digitalWrite(AIN1, LOW);  //set pin 1 to low
  digitalWrite(AIN2, LOW);  //set pin 2 to low
  //right motor stop
  digitalWrite(BIN1, LOW);  //set pin 1 to low
  digitalWrite(BIN2, LOW);  //set pin 2 to low
}

//robot forward function
void fwd(int speed) {
  allLedsOff();
  digitalWrite(grnLED, HIGH);
  digitalWrite(AIN1, HIGH);       //set pin 1 to high
  digitalWrite(AIN2, LOW);        //set pin 2 to low
  digitalWrite(BIN1, HIGH);       //set pin 1 to low
  digitalWrite(BIN2, LOW);        //set pin 2 to high
  analogWrite(PWMA, abs(speed));  //set forward speed
  analogWrite(PWMB, abs(speed));  //set forward speed
}

//robot reverse function
void rev(int speed) {
  allLedsOff();
  digitalWrite(redLED, HIGH);
  digitalWrite(AIN1, LOW);        //set pin 1 to low
  digitalWrite(AIN2, HIGH);       //set pin 2 to high
  digitalWrite(BIN1, LOW);        //set pin 1 to low
  digitalWrite(BIN2, HIGH);       //set pin 2 to high
  analogWrite(PWMA, abs(speed));  //set reverse speed
  analogWrite(PWMB, abs(speed));  //set reverse speed
}

//robot spin function
void spin(int speed, int dir) {
  allLedsOff();
  if (dir > 0) {
    digitalWrite(bluLED, HIGH);
    digitalWrite(AIN1, LOW);   //set pin 1 to low
    digitalWrite(AIN2, HIGH);  //set pin 2 to high
    digitalWrite(BIN1, HIGH);  //set pin 1 to low
    digitalWrite(BIN2, LOW);   //set pin 2 to high
  } else {
    digitalWrite(ylwLED, HIGH);
    digitalWrite(AIN1, HIGH);  //set pin 1 to low
    digitalWrite(AIN2, LOW);   //set pin 2 to high
    digitalWrite(BIN1, LOW);   //set pin 1 to low
    digitalWrite(BIN2, HIGH);  //set pin 2 to high
  }
  analogWrite(PWMA, abs(speed));  //set reverse speed
  analogWrite(PWMB, abs(speed));  //set reverse speed
}

//robot turn function
void turn(int speed, int dir) {
  allLedsOff();
  digitalWrite(AIN1, HIGH);  //set pin 1 to low
  digitalWrite(AIN2, LOW);   //set pin 2 to high
  digitalWrite(BIN1, HIGH);  //set pin 1 to low
  digitalWrite(BIN2, LOW);   //set pin 2 to high
  if (dir > 0) {
    digitalWrite(bluLED, HIGH);
    analogWrite(PWMA, robotSpeed * 1.5);
    analogWrite(PWMB, robotSpeed * 0.5);
  } else {
    digitalWrite(ylwLED, HIGH);
    analogWrite(PWMA, robotSpeed * 0.5);
    analogWrite(PWMB, robotSpeed * 1.5);
  }
}
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

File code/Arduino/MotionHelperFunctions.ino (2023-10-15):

//turn all the LEDS off
void allLedsOff () {
  for (int i = 0; i < 4 ; i++) {
    digitalWrite(ledPins[i], LOW);
  }
}

//get sonar distance
float getDistance(int *x, int *y)
{
  float echoTime;                   //variable to store the time it takes for a ping to bounce off an object
  float calculatedDistance;         //variable to store the distance calculated from the echo time
  int trigPin = *x;
  int echoPin = *y;
  //send out an ultrasonic pulse that's 10ms long
  digitalWrite(trigPin, HIGH);
  delayMicroseconds(10);
  digitalWrite(trigPin, LOW);

  echoTime = pulseIn(echoPin, HIGH);      //use the pulsein command to see how long it takes for the
  //pulse to bounce back to the sensor

  calculatedDistance = echoTime / 148.0;  //calculate the distance of the object that reflected the pulse (half the bounce time multiplied by the speed of sound)

  return calculatedDistance;              //send back the distance that was calculated
}

//robot stop function
void stop() {
  allLedsOff();
  //left motor stop
  digitalWrite(AIN1, LOW);                          //set pin 1 to low
  digitalWrite(AIN2, LOW);                          //set pin 2 to low
  //right motor stop
  digitalWrite(BIN1, LOW);                          //set pin 1 to low
  digitalWrite(BIN2, LOW);                          //set pin 2 to low
}

//robot forward function
void fwd(int speed) {
  //digitalWrite(redLED, HIGH);
  digitalWrite(AIN1, HIGH);                         //set pin 1 to high
  digitalWrite(AIN2, LOW);                          //set pin 2 to low
  digitalWrite(BIN1, HIGH);                         //set pin 1 to low
  digitalWrite(BIN2, LOW);                        //set pin 2 to high
  analogWrite(PWMA, abs(speed));    //set forward speed
  analogWrite(PWMB, abs(speed));    //set forward speed
}

//robot reverse function
void rev(int speed) {
  //digitalWrite(bluLED, HIGH);
  digitalWrite(AIN1, LOW);                         //set pin 1 to low
  digitalWrite(AIN2, HIGH);                        //set pin 2 to high
  digitalWrite(BIN1, LOW);                         //set pin 1 to low
  digitalWrite(BIN2, HIGH);                        //set pin 2 to high
  analogWrite(PWMA, abs(speed));    //set reverse speed
  analogWrite(PWMB, abs(speed));    //set reverse speed
}

//robot spin function
void spin(int speed, int dir) {
  //digitalWrite(grnLED, HIGH);
  if (dir > 0) { //spin right
    digitalWrite(AIN1, HIGH);                         //set pin 1 to low
    digitalWrite(AIN2, LOW);                        //set pin 2 to high
    digitalWrite(BIN1, LOW);                         //set pin 1 to low
    digitalWrite(BIN2, HIGH);                        //set pin 2 to high

  } else { //spin left
    digitalWrite(AIN1, LOW);                         //set pin 1 to low
    digitalWrite(AIN2, HIGH);                        //set pin 2 to high
    digitalWrite(BIN1, HIGH);                         //set pin 1 to low
    digitalWrite(BIN2, LOW);                        //set pin 2 to high
  }
  analogWrite(PWMA, abs(speed));    //set left wheel speed
  analogWrite(PWMB, abs(speed));    //set right wheel speed
}

//robot turn function
void turn(int speed, int dir) {
  //digitalWrite(redLED, HIGH);
  //digitalWrite(bluLED, HIGH);
  digitalWrite(AIN1, HIGH);                         //set pin 1 to low
  digitalWrite(AIN2, LOW);                        //set pin 2 to high
  digitalWrite(BIN1, HIGH);                         //set pin 1 to low
  digitalWrite(BIN2, LOW);                        //set pin 2 to high
  if (dir > 0) {//turn right
    analogWrite(PWMA, robotSpeed * 1.5);   //left wheel
    analogWrite(PWMB, robotSpeed * 0.5);   //right wheel
  }
  else {//turn left
    analogWrite(PWMA, robotSpeed * 0.5);   //left wheel
    analogWrite(PWMB, robotSpeed * 1.5);    //right wheel
  }
}

//robot pivot function
void pivot(int speed, int dir) {
  //digitalWrite(bluLED, HIGH);
  //digitalWrite(grnLED, HIGH);
  digitalWrite(AIN1, HIGH);                         //set pin 1 to low
  digitalWrite(AIN2, LOW);                        //set pin 2 to high
  digitalWrite(BIN1, HIGH);                         //set pin 1 to low
  digitalWrite(BIN2, LOW);                        //set pin 2 to high
  if (dir > 0) {//pivot right
    analogWrite(PWMA, abs(speed));  //left wheel
    analogWrite(PWMB, 0);           //right wheel
  }
  else { //pivot left
    analogWrite(PWMA, 0);          //left wheel
    analogWrite(PWMB, abs(speed)); //right wheel
  }
}

void randomWander(){      //function to move robot random forward and turn
  Serial.println("randomWander()");
  int randNumber = random(millis());    //generate a random number
  int distance = randNumber % 50;       //limit the values between 0 and 50 cm
  int angle = randNumber % 90;          //limit the values between 0 and 90 degrees
  Serial.print(distance);
  Serial.println(" deg\t");
  Serial.print(angle);
  Serial.print(" cm\t");
  fwd(robotSpeed);
  delay(distance);
  turn(angle,robotSpeed);
  delay(distance);
}

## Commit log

2022-08-06 /parts
    All these parts need to be 3d printed to build the Lily-bot
    [GP2Y0A21YK0F IR sensor mt - PRINTx4.stl, HC-SR04 sonar sensor mounts - PRINTx4.stl, Lily-Bot Chassis Standoffs (HEX) - PRINTx4.stl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]
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2022-08-11 Version 2 of IR mount, motor mount, lower chassis
    See revisions for 8/11/22 text file
    [GP2Y0A21YK0F IR sensor mt - v2.stl, Lily-Chassis-Bottom-v2.stl, Motor Mount - V2.stl]
2022-08-13 Motor Mount-V3 adds lip to mount to fix wheels flaring
    [Motor Mount-V3.stl]
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2022-08-13 /parts
    V2 of mounts to fix motor flaring and screw hole size
    V2 of chassis to fix aster wheels dragging
    [GP2Y0A21YK0F IR sensor mt - V2.stl, Lily-Bot Bottom Chassis - V2.stl, Motor Mount-V2.stl]
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2022-09-04 /parts
    updated Daisy∞bot bottom chassis to fix caster wheel size and location of side wheels
    updated Lily∞bot top chassis to move over and angle more to accomodate breadboard and power chord and USB chord
    [Daisy-Bottom STL.obj, Lily-Top STL.obj]
2022-09-28 /parts
    V3 of top chassis removes square outline for Uno Microcontroller
    Square standoff is 8mm x 8 mm with 2.9 mm screw hole
    [LilyBot Standoffs Square.stl, Lily∞Bot top chassis_v3.stl]
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2022-12-17 Updated GCODE files for lily. Changed size of Rosie 12in-->11.75in. Deleted extra files
    [New Rosie bottom.SLDPRT, New Rosie bottom.STL, New Rosie top.SLDPRT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]
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2023-01-11 Flipped motor mounts print files (wrong orientation)
    [Motor Attachment .3mf]
2023-01-18 Tight motor mount and added griper
    Changed motor mount tolerance to make it tighter. Also added the downloaded files for the gripper
    [Gripper mount.SLDPRT, Gripper.3mf, LilyBot.SLDASM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]
2023-01-18 Daisy standoff hole
    I moved the standoff holes closer to the center so they would not interfere with the motor.
    [Copy of Daisy∞Bot top chassis.stl, Daisy bottom.3mf, Daisy bottom.SLDPRT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]
2023-01-18 Motor mount fix
    Some of the daisy chassis were did not have enough space between the motors and the standoffs. So I design a little extension for the motors
    [Gripper mount.SLDPRT, Motor Attachment .SLDPRT, Motor mount fix.3mf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]
2023-01-18 Jetson Nano, full tray and motor mount fix v2
    Made assembly of jetson nano version of daisy.
    Created a printer file full of motor mounts.
    Fixed the motor mount fix
    [032-0256-000_1.step.SLDPRT, 0402_H040.step.SLDPRT, 0402_H060.step.SLDPRT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]
2023-01-18 Full tray of all attachment
    Printer files with attachment covering the entire tray to print faster
    [12xSonar sensor Attachment .3mf, 18xIR sensor Attachment .3mf, IR sensor Attachment .3mf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]
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2023-01-23 Lily standoffs
    Created the files for Lily standoffs with 25 of them
    [25xLilyBot Standoffs3mf.3mf]
2023-01-26 Standoff hole 2.9 --> 3.0mm
    We found the standoffs to be very hard to screw in so I increased 0.1mm the diameter of the hole.
    [25xDaisyBot standoff.3mf, Daisy standoff.STL, DaisyBot standoff Square.stl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]
2023-01-26 Chip holder for lily and daisy
    The daisy holes for the mega chip did not fit completely so I adjusted it to fit.
    On the lily, the holes were too shallow to firmly attach chip so I made them deeper.
    [Daisy top.3mf, Daisy top.SLDPRT, Daisy top.STL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]
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2023-02-02 Aligned Daisy letters created BOM
    The daisy letters were off by 90 degrees so I changed the daisy top. I also made the letters from the bottom bigger to match top.
    I created the file for the BOM
    [BOMLily.xlsx, Daisy bottom.3mf, Daisy bottom.SLDPRT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]
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2023-02-11 Changed gap in attachment hook to 4.1mm
    The part on the attachments that looks like an arrow has a gap o 4.1mm
    [16xMotor Attachment .3mf, 16xMotor Attachment Twins.3mf, 20xMotor Attachment Twins.3mf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]
2023-02-24 Create DaisyBot-buzzer.ino
    Code to enable Daisy Bot to play sounds on a buzzer
    [DaisyBot-buzzer.ino]
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2023-03-07 Created new motor mounts
    New motor mounts will be bolted to the bottom.
    Just made the files for the lily.
    [Lily Bottom.3mf, Lily Bottom.STL, New Lily Bottom.3mf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]
2023-03-09 Final motor mount and organized files
    Uploaded the last version of the motor mounts. The file contains one right and one left mount.
    I also deleted some obsolete files from GitHub and added the caster levels.
    [15xcasterLevel.3mf, Attachment Test 4-5mm.STL, Attachment head.STL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]
2023-03-14 Implemented new motor mounts to lily and Daisy bottom
    Changed the design slightly for the new motor mounts to make them fit tighter and added the holes to attach it to Lily and Daisy with a little mark to guide it.
    [Daisy bottom.3mf, Daisy bottom.SLDPRT, Daisy bottom.STL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]
2023-03-14 New gripper and cleaning
    Uploaded the new gripper files with the attachment.
    Cleaned old files
    [Attachment Test 4mm.SLDPRT, Attachment head.SLDPRT, Gripper Attachment_v1.SLDPRT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]
2023-03-16 fixed new motor mount, new battery holder
    Change the new motor mount slightly. Started adjusting the spiral attachment. Started concept for battery holder
    [Lily Bottom.SLDPRT, Lily top.SLDPRT, New Motor Mount.SLDPRT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]
2023-03-21 Battery attachment and spiral pocket
    First design for battery holder finished on lily and started on daisy.
    Changed all the spiral attachment to have a pocket. All attachments should have a 4.1mm gap to fit tightly in the 4.50mm spiral.
    [Daisy bottom.SLDPRT, Daisy bottom.STL, Daisy top.3mf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]
2023-03-31 New battery attachments and removed pockets
    Added more battery attachments to Lily and Daisy.
    Also removed pockets from spiral attachments.
    Modified ToF sensor to 4.1mm attachment.
    [Daisy 9V Battery Holder.3mf, Daisy 9V Battery Holder.SLDPRT, Daisy 9V Battery Holder.STL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]
2023-04-04 Battery holder fixed holes
    [032-0256-000_1.step.SLDPRT, 0402_H040.step.SLDPRT, 0402_H060.step.SLDPRT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]
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2023-04-06 Updated Rosie
    Added the new battery attachments to Rosie design. 1 9V battery and 1 4xAA battery
    [New Rosie bottom.SLDPRT, New Rosie bottom.STL, New Rosie top.SLDPRT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]
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2023-05-11 Chip holder new gen
    To improve flexibility on which chip it uses, the chip holder will be held in a different piece. The top chassis will simply have a hole.
    [Lily top.SLDPRT, LilyBot.SLDASM, Lt. Motor Mount.SLDPRT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]
2023-05-11 Pico and Nano tops
    I created the tops for Lily Nano and Pico. Started printing them.
    [Lily Bottom(old).SLDPRT, Lily Bottom.SLDPRT, Lily top.3mf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]
2023-05-16 Fixed modular controller. Started modular battery
    In order to be able to switch between the different controllers (UNO, Mega, nano, pico etc) I created a modular top that can screw and unscrew a piece of it.
    For the battery it is a similar concept, in order to be able to switch between different casings, I just created an individual module.
    [Battery holder.SLDPRT, Nano_Top.3mf, Nano_Top.SLDPRT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]
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2023-05-18 List of materials for Lily and changed UNO top
    Created an excel file to count the materials needed for any number of lilyBots. Also one for specifically 36 with the current materials available.
    Changed the UNO top so is is straight and sensors can fit.
    [36 Lily order.xlsx, Calculator Lily materials.xlsx, Uno_Top.3mf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]
2023-05-23 Modular tops and filet on battery holder
    Expanded the modular design of the top to daisy and Rosie. Included Mega and Jetson Nano.
    Fileted the battery cage to increase strength.
    [Daisy bottom.3mf, Daisy bottom.SLDPRT, Daisy bottom.STL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]
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2023-05-25 New snap on for Mega
    Continue working on modular tops. Trying to make all chips snap on.
    Daisy and Lily tops should have same size of holes while rosie will have slightly bigger
    [12xSonar sensor Attachment .3mf, 15xcasterLevel.3mf, 18xIR sensor Attachment .3mf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]
2023-05-26 Snap on tops and Lily assembly
    Made snap on tops for Uno Mega and Pico. Tested and refined Pico one. Fixed lily assembly
    [9V Battery Holder.SLDPRT, Battery holder.SLDPRT, Gripper attachment.SLDPRT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]
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2023-09-19 Back from Summer
    Fixed up the designs don by Dr. Berry:
    9V battery holder
    Pico battery holder
    Microbit battery holder
    MicroBit top module
    [9V Battery Holder New.SLDPRT, 9V Battery Holder New.STL, MicroBit_Module.SLDPRT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]
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2023-09-22 Organized files
    Organized the top modules and battery holders n their own folder.
    Created printer files for all new models
    [9V Battery Holder New.SLDPRT, 9V Battery Holder New.STL, 9V Battery Holder.SLDPRT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]
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2023-10-15 updated fritzing files, code for Raspberry PI Pico W
    updated fritzing files, code for Raspberry PI Pico W
    [LilyPicoFritzBuzzer.fzz, LilyPicoWFritzButton.fzz, LilyPicoWFritzExternalLED.fzz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]
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2023-12-03 assembly instructions added
    add folder for assembly instruction and added assembly instructions
    [Lt. Motor Mount.SLDPRT, Rt. Motor mount.SLDPRT, Small breadboard.SLDPRT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]
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2024-04-15 Motor snap testing
    [Lily Bottom Flex V5.SLDPRT, LilyBot - Reduced Hardware.SLDASM]
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
